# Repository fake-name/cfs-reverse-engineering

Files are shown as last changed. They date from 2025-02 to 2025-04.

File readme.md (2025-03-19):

Creality CFS Filament system Reverse Engineering

This is part of an effort to use the Creality CFS feeder system as a general AMS system for any Klipper-based printer.

This *should* be trivial, as the printer this normally interoperates with is also a Klipper-based machine. However, as usual, Creality are violating the GPL by not releasing their changes and additions to klipper (Creality implemented a custom bus type, and a bunch of utility bits to talk to the filament box).

Given that, the other option is reverse engineering how the feeder works. Fortunately, that should be pretty straightforward for most of the bits.

Anyways, high resolution board images are [here](PCBs.md).

Some attempts at analyzing the various binary firmware and python objects are [here](firmware.md)

Overall system structure:



The board can be flashed with klipper by just treating it as having a STM32F106VET6 (which is binary compatible with the GD32F303VET6). You loose a bit of potential clock-rate by not doing giga-device specific stuff, but this is fairly slow anyways so it should be fine. 

Specifying the klipper host connection to be on PA2/PA3 even works (albeit with RS485).

Current plan to convert the system to klipper in a neat way involves a simple interposer board to re-purpose the RS-485 lines:



The adapter board sits between the existing rear-panel connector and the existing controller board. It basically has 3 connectors, a CAN transciever, and a bypass capacitors. It simply carries all other signals + power through the PCB, but replaces the two RS-485 lines with CAN signalling. 

Since the IO needed to drive a CAN interface is exposed on the unused "J10" connector, that is connected to an appropriate CAN bus transciever IC (a [TCAN332G](https://www.ti.com/lit/ds/symlink/tcan332g.pdf)). 

The other end is another custom PCB. In this case, it's another custom PCB heavily inspired by the [candleLight FD](https://linux-automation.com/en/products/candlelight-fd.html) (read: I used some of their schematics for a starting point, the entire layout is my own work). It breaks out the CFS bus to a usb-CAN adapter (via [candleLight_fw](https://github.com/candle-usb/candleLight_fw) and the 24V power in via either a DC Barrel jack or a 2-pin micro-fit connector (there are pads for both on the PCB).

It also has a pair of LEDs to indicate buffer status, and some activity LEDs. 

Both boards are up at [Adapter](~/Adapter/). License for them is GPL3, since the candleLight FD is GPL3.

I had JLCPCB do the PCBs, they work out to ~$7 ea (CAN Adapter) and ~$10 ea (CFS-Bus Adapter), at qty 5 of each. I'm also trying LCSC's [custom-cable service](https://www.lcsc.com/customcables?utm_source=customcables&utm_medium=navbar) to make the short interposing cables, which wound up being ~$50 for 10 of each.

Full production files for each of the PCBs are in the respective folders, they should drag & drop into JLCPCB's PCBA service. The cables are based on a lot of guesswork about what the right connectors are, once I confirm I have the right part-numbers, I'll document that here as well.

Note that immediately after ordering the CFS-Bus-Adapter, I realized it would be super neat to allow the CAN transciever to be either connected to the CAN peripheral in the MCU (which is how it is now), and a UART interface. That would let this interact with the existing firmware if/when it get's properly reverse engineered, or Creality finally stops violating the GPL and provides the source for their [distributed-in-compiled-form-only klipper extensions](https://github.com/Guilouz/Creality-K2Plus-Extracted-Firmwares/tree/main/Firmware/usr/share/klipper/klippy/extras) (see all `.so` files, which are compiled with cython to make them opaque).

------

First rev board issues:

 - Pinout on J3 for CFS Can adapter board is reversed.   
   This can be fixed by just mirroring the routing of the jumper cable.
 - The open-collector buffer signals have pullups to 5V in the buffer. That means the buffer status LED resistors as implemented (i.e. between 24V and the buffer status pins) are effectively always on, since the 5V pullup winds up sinking current from the 24V LED rail.   
   This needs to be fixed by rev-ing the board (or with track hackery). Right now, the CFS buffer just changes the LED brightness, rather then turning them on and off.

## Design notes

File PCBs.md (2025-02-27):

# CFS Internal PCBs

## Main Motherboard
  
  

RS485 interface [3Peak TPT75176H](https://www.3peak.com/rs485/tpt75176h)
  

DC Motor Drivers: [HTD8236](https://offer-product.oss-cn-beijing.aliyuncs.com/product/offer/attachment/null/file/subPdf_749347_333113_20240123-141150640.pdf)
The use of the [LM358](https://www.ti.com/product/LM358) op amps are a mystery. Possibly current sensing? That would also align with the presence of the `R500` 500 mΩ resistors.   
Also present: a AMS1117 3.3v linear regulator. 
  

[24C16F EEPROM](https://ww1.microchip.com/downloads/en/DeviceDoc/Atmel-8719-SEEPROM-AT24C16C-Datasheet.pdf) in a SOT23-5 package.  
Q10 is probably a switch for the LCD's backlight LED?
  

Main CPU: [GD32F303](https://www.gigadevice.com/product/mcu/main-stream-mcus/gd32f30x-series/gd32f303) - STM32 ripoff ARM.
  

Brushless motor driver - [MS8828](https://www.relmon.com/en/index.php/list/detail/300.html). Made by [Ruimeng TECHNOLOGY](https://www.relmon.com)(sic). This part is interesting, because the firmware has references to a different part in some strings in it (`MS3791`)
  

## Pinouts:

### Connector types:
The majority of the connectors on the PCB are variants of the JST ["GH" connector style](https://www.jst.com/products/crimp-style-connectors-wire-to-board-type/gh-connector/), though not likely actually made by JST. 

All connectors other then the RS-485/Power (J4), the LCD (J15) and the filament monitor (J6) are GH-style. This includes the feeder motor connector (J5) which is indeed a GH connector, though with a right-angle-mount PCB connector.

##### J10 "Address" connector (not used?)

This connector is particularly interesting, since it is unused in the CFS configuration, and exposes the USB pins of the MCU. That means it should be possible to make up a USB cable. Alternatively, it also exposes the CAN pins.

The USB interface is annoying in that the MCU documentation specifies approximately 50Ω series termination resistors on both the DM and DP pins, which are not present. It may be possible to add these resistors in-line with the cable. I need to do some experiments.

PA4,6,7 don't have any features that seem to make them of particular interest. 

Annoyingly, the Gigadevices USB interface documentation is really terrible, and you also need a 1.5KΩ resistor between D+ and VCC (or a MCU IO pin). Once I added that (to PC6), and told klipper to pull the pin high at boot, the USB interface started working.

| Pin #  |  Function | MCU Pin No | Logical Pin | Note |
| ---| --- | --- | --- | --- |
| 1 | power | 3.3V | | |
| 2 | | P.70 | PA11 | USBDM / CAN0_RX |
| 3 | | p.71 | PA12 | USBDP / CAN0_TX |
| 4 | | p.31 | PA6 | |
| 5 | | p.32 | PA7 | |
| 6 | | p.29 | PA4 | |
| 7 | power | GND | | |

##### J4 (Power/Comm Connector)
 
| Pin #  | Function | MCU Pin No | Logical Pin |
| --- | --- | --- | --- |
| 1 | +24V | n/a | |
| 2 | +24V | n/a | |
| 3 | GND | n/a | |
| 4 | GND | n/a | |
| 5 | RS485-B | see note | |
| 6 | RS485-A | see note | |
| 7 | Filament Buffer SW 1 | p.55 | PD8 |
| 8 | Filament Buffer SW 2 | p.56 | PD9 |
The 485 bus uses 3 pins:
 
 - P.25 (PA2) - TX Enable/RX Disable - 2N7002 translator
 - P.26 (PA3) - RX
 - TX - I think strapped to ground. 

This is I believe technically violating RS-485 specs.

This device, like many crappy chinese "RS-485" systems, does not *really* support RS485. Instead, the bus is run in a pseudo-differential-open-collector mode (much like CAN networks), in that the transmitter is permanently wired up as "transmitting", e.g. the "space" mode, and rely on the bus termination resistors to drive the bus back to the idle "mark" state. Aside from not being real RS-485, this STRONGLY limits the maximum baud-rate the bus due to the fact that the only termination resistors present on the PCB are two 300Ω resistors, with `A` pulled to VCC (5V) and `B` pulled to ground.

While there is a provision for a 120Ω termination resistor on the board, it is not loaded on the board I have.

I *believe* this connector is a SMW200-08, (Yeonho SMW). 

It is a 2 mm pitch, latching connector, and the full-width latch catch on the PCB-mount connector is fairly distinct.

##### J15 (FP LCD Connector)

| Pin #  |  Function | MCU Pin No | Logical Pin |
| ---| --- | --- | --- |
| 1 | power | 3.3V | |
| 2 | power | GND | |
| 3 | | p.16 | PC1 |
| 4 | | p.17 | PC2 |
| 5 | | p.18 | PC3 |
| 6 | | p.33 | PC4 |
| 7 | backlight | P.35 | PB0 |

Note: The backlight pin is a open collector transistor.

I *believe* this connector is a SMW200-07, (Yeonho SMW). 

It is a 2 mm pitch, latching connector, and the full-width latch catch on the PCB-mount connector is fairly distinct.

The power-in connector (J4) is the same series.

##### J7 Front-Panel LED PCB Connector

| Pin #  |  Function | MCU Pin No | Logical Pin | Function |
| ---| --- | --- | --- | --- |
| 1 | power | 5.0V | | |
| 2 | | p.63 | PC6 | Slot 1 Red LED |
| 3 | | p.93 | PB7 | Slot 1 White LED |
| 4 | | p.64 | PC7 | Slot 2 Red LED |
| 5 | | p.90 | PB4 | Slot 2 White LED |
| 5 | | p.65 | PC8 | Slot 3 Red LED |
| 6 | | p.91 | PB5 | Slot 3 White LED |
| 7 | | p.66 | PC9 | Slot 4 Red LED |
| 8 | | p.92 | PB6 | Slot 4 White LED |
| 10 | power | GND | | |

Note: All LED connectors are Open-Collector Transistors.
Presumably, the LEDs are between 5V and the various open-collector
outputs.

Interestingly, the red LEDs for slots 2 & 3 seem to be the same pin. 

This is a 10 pin connector, but I somehow missed a pin somewhere. 

##### Motor driver pins

|  Driver pin  | M1 | M2 | M3 | M4 |
| --- | --- | --- | --- | --- |
| IN 1 | p.84 (PD3) | p.82 (PD1) | p.62 (PD15) | p.60 (PD13) |
| IN 2 | p.83 (PD2) | p.81 (PD0) | p.61 (PD14) | p.59 (PD12) |

##### Current Feedback Pins

| Motor |  Pin | Logical Pin |
| --- | --- | --- |
| M1 | p.34 | PC5 |
| M2 | p.15 | PC0 |
| M3 | p.24 | PA1 |
| M4 | p.23 | PA0 |

Each feedback pin is driven by an op-amp with some gain and a offset shift.

##### Brushed Motor connector / J5

| Pin #  |  Function | MCU Pin No | Logical Pin |
| ---| --- | --- | --- |
| 1 | I2C? | P.79 |  PC11 |
| 2 | Power | GND | |
| 3 | I2C? | p.80 |  PC12 |
| 4 | | p.88 |  PD7 |
| 5 | | p.87 |  PD6 |
| 6 | | p.86 |  PD5 |
| 7 | | p.85 |  PD4 |
| 8 | Power | 5V | |
| 9 | | M4-Out1 | |
| 10 | | M4-Out2 | |
| 11 | | M3-Out1 | |
| 12 | | M3-Out2 | |
| 13 | | M2-Out1 | |
| 14 | | M2-Out2 | |
| 15 | | M1-Out1 | |
| 16 | | M1-Out2 | |

Pins 1 & 3 have 2N7002 discrete level translators to go from 5V I2C to 3.3V MCU I2C, I believe. They connect thru to the Temp/Humidity measurement I2C sensor in the chamber. 

##### RFID Readers / J8 / J1

| Pin #  |  Function | J8 | J19 |
| ---| --- | --- | --- |
| 1 | Power | 3.3V | |
| 2 | I2C? | p.48 (PB11) | p.96 (PB9)  |
| 3 | Power | GND | |
| 4 | I2C? | p.47 (PB10) | p.95 (PB8)  |
| 5 | Power | GND | |
| 6 | | N/C? | |

Pin 6 on both seems to be not-connected, surprisingly.

##### J6 - Odometer and second-stage filament presence detector

| Pin #  |  Function | MCU Pin No | Logical Pin |
| ---| --- | --- | --- |
| 1 | Power | 3.3V | |
| 2 | | p.46 |  PE15 |
| 3 | | p.53 |  PB14 |
| 4 | | p.54 |  PB15 |
| 5 | | p.52 |  PB13 |
| 6 | | p.51 |  PB12 |
| 7 | | p.89 |  PB3 |
| 8 | Power | Gnd | |
| 9 | | p.38 |  PE7 |
| 10 | | p.39 |  PE8 |
| 11 | | p.40 |  PE9 |
| 12 | | p.41 |  PE10 | 

Pins 9-12 have R/C filters on them. My current guess is they are 
the filament presennce paths, while the other 6 are for the odometer.

Hopefully I can extend https://github.com/Klipper3d/klipper/pull/5369 to support the odometer.

##### BLDC Motor Driver:

| Driver Func | MCU Pin No | Logical Pin |
| --- | --- | --- |
| SS | p.03 | PE4 |
| FG | p.42 | PE11 |
| F/R | p.02 | PE3 |
| PWM | p.44 | PE13 |

FG is a tachometer output from the driver. SS is motor brake, F/R is forward/reverse, PWM is speed control (obviously).

### RFID Readers:

[FM17622](https://eng.fmsh.com/AjaxFile/DownLoadFile.aspx?FilePath=/UpLoadFile/20190410/FM17510_ps_eng.pdf&fileExt=file) - Supports most protocols and interfaces. 13.56 MHz (I think?)
  

  

Both RFID readers are identical.
  

### LCD 

Front-Panel LCD - [TM1621B](https://wmsc.lcsc.com/wmsc/upload/file/pdf/v2/lcsc/2209231730_TM-Shenzhen-Titan-Micro-Elec-TM1621B_C5174490.pdf) - Stand-Alone LCD driver, no MCU. 
  

### Connector PCB
  

Cable colors

 - Yellow - 24V
 - Green - GND
 - Blue - 485
 - Red - 485
 - White - sw?
 - Black - sw?

### Filament sensor PCB

Forgot to take pictures of the other side of the board.
  

### Filament feeder assembly

This is partly a pass-thru to the filament sensor PCB (above). 

It also has a MagnTek [MT6826S](https://www.magntek.com.cn/upload/pdf/202407/MT6826S_Datasheet_Rev.1.1.pdf). 
  

  

### Filament 4-into-1 buffer PCB.
  
  

The 4-into-1 PCB is very dumb, it just has 2 open-collector outputs that correspond to each optointerruptor. One for each end of the buffer-state.

All the parts on the board are just a DC-DC converter to produce a local power supply from the 24V bus. 

Since all CFS boxes will have access to the buffer state pins, whichever one is currently active in feeding to the print head can autonomously keep the buffer loaded without needing the printer controller's involvement.

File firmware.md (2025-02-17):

Firmwares:

MCU Firmware files are taken from [here](https://github.com/Guilouz/Creality-K2Plus-Extracted-Firmwares/tree/main/Firmware/usr/share/klipper/fw/cfs). In particular, I'm examining `cfs0_050_G32-cfs0_000_113.bin`, admittedly for no particular reason other then it seems the most current version.

Just throwing the firmare into `strings already produces a LOT of really interesting snippets:

```
 \ | /
- RT -     Thread Operating System
15:19:29
Jan  6 2025
 / | \     %d.%d.%d build %s %s
 2006 - 2022 Copyright by RT-Thread team
```
Interestingly, the MCU does not run a klipper based system. Instead, it seems to be based on RT-Thread, which is a primarily Chinese-origin RTOS. 

RT-Thread is apache licensed (not copyleft), but it does require attribution, and interestingly searching for `"creality" "rt-thread"` returns no meaningful results, so creality seems to have managed to even violate a bsd-style license!

Ghidra gives us the full version info:

```
    debug_print(s_\_|_/_08018378);
    debug_print(s_-_RT_-_Thread_Operating_System_08018384);
    debug_print(s_/_|_\_%d.%d.%d_build_%s_%s_080183c0,5,0,2,s_Jan_6_2025_080183b4,s_15:19:29_080183a8);
    debug_print(s_2006_-_2022_Copyright_by_RT-Thre_080183e4);
```

So this is based on RT-thread 5.0.2, built on `Jan_6_2025` at `15:19:29`. 5.0.2 was released
on Oct 7, 2023, so they're a bit behind in updating the copyrights in the code if nothing else.

There's also a LOT of debug/informational statements:

```

feeder reverse detooth slot_id:%d
hub reverse update [dir:%s, speed:%d]
feeder reverse detooth force
detooth update [dir:%s, speed:%d]
MS3791 is overload
motor_blocked_detect_timer
pull back hub PE retry:%d
pull back hub PE timeout, retry times exhausted
times:%d, %d error,T%d AT8236 and MS3791 push filament timeout
#<times:%d, %d error,T%d pull_back_hub motor block, state=%02x
perhaps pull back odometer
already pull back odometer
etc...
```

In particular, there appear to be at least the remaining stubs of a interactive interface:

```
slot%d read rfid and margin estimation
preloading
read
enable
disable
aging
Usage: 
preloading enable            - enable preloading
preloading disable           - disable preloading
preloading aging             - aging preloading
preloading read [slot_id]    - read filament info
```

```
Usage: 
bl24cxx init                            - init bl24cxx
bl24cxx capacity                        - bl24cxx get capacity
bl24cxx ready                           - bl24cxx is ready?
bl24cxx deadlock <address>              - bl24cxx deadlock
bl24cxx undeadlock                      - bl24cxx undeadlock
```

```
Usage: 
odo_mag init            - init magnetic odometer
odo_mag test            - test magnetic odometer communication
odo_mag monitor [en]    - print magnetic odometer positon
odo_mag reset           - reset magnetic odometer
odo_mag read step       - read raw value of magnetic odometer
odo_mag read mm         - read position of magnetic odometer
```

Having what are basically help strings in the generated firmware image is interesting. 

There are also a number of situations where there are strings with VT100 control characters in them:`[31m[E/odometer_magnetic]`, `[0m[D/odometer_magnetic]`, `[31m[E/preloading]`, etc... I suspect there may be a debug UART somewhere.

It seems unlikely to me that all the debug strings are fed back over the RS485 port, in particular considering that there can be up to 4 of these things sharing a single RS485 bus. 

There's also some super weird stuff:

`database checksum error, load default value ...`

I have no idea what a "database" would be in the context of a embedded MCU with no real storage space. My best guess is it's something related to the I2C EEPROM. There are also supporting strings: `read_motor_info eeprom                  - read motor block info from eeprom`.

I suspect there are a number of locations where weird terminology is more a function of poor translation. There are a lot of references to `<something>_aging` in various places, which I suspect may be ore accurately stated as a timeout or latency.

------

So I've been going through and naming function stubs, working through the decompilation of the MCU source, and things are starting to make some sense. They are definitely measuring the motor current for the brushed DC motors:

```
        rt_kprintf(s_current_channel_=_%d_0800445b + 1,uVar3);
        FUN_080073e8();
        FUN_0800c0fc(0xff);
        iVar1 = _DAT_08004474;
        while (fVar5 = (float)FUN_0800725a(), iVar2 = _DAT_08004490, (int)ABS(fVar5) < iVar1)
        {
            iVar2 = FUN_08003aa8(uVar3,0,5);
            if (iVar2 != 0)
            {
                rt_kprintf(s_AT%d_pull_out,_restart_08004476 + 2,uVar3);
                FUN_0800c130();
                goto LAB_0800425c;
            }
            FUN_08019cc0(10);
        }
```

------

Empirically, connecting to the MCU with a debugger and poking it while it's running let's me determine whether it's primarily running from main flash (`0x0800_0000`), rather then the mirror (`0x0000_0000`). 

```
0x0800066e in ?? ()
─── Assembly ──────────────────────────────────────────────────────────────────────────
 0x0800066e  ? ldr      r0, [r1, #0]
 0x08000670  ? str      r2, [r1, #0]
 0x08000672  ? cmp      r0, r2
 0x08000674  ? ittt     hi
 0x08000676  ? ldrhi    r0, [r3, #0]
 0x08000678  ? addhi.w  r0, r0, #16777216       ; 0x1000000
 0x0800067c  ? strhi    r0, [r3, #0]
 0x0800067e  ? ldr      r0, [r3, #0]
 0x08000680  ? movw     r3, #15000      ; 0x3a98
 0x08000684  ? udiv     r0, r0, r3
─── Breakpoints ───────────────────────────────────────────────────────────────────────
─── Expressions ───────────────────────────────────────────────────────────────────────
─── History ───────────────────────────────────────────────────────────────────────────
─── Memory ────────────────────────────────────────────────────────────────────────────
─── Registers ─────────────────────────────────────────────────────────────────────────
       r0 0x000009d4        r1 0x20000b28          r2 0x0040103b        r3 0x20000c80
       r4 0x00007530        r5 0x20000010          r6 0x20000918        r7 0x08002224
       r8 0x08002208        r9 0x08002224         r10 0x00000001       r11 0x00000002
      r12 0x00ffffff        sp 0x2000fef0          lr 0x08001437        pc 0x0800066e
     xPSR 0x01000000     fpscr 0x00000000         msp 0x2000fef0       psp 0x20003af8
  primask 0x00         basepri 0x00         faultmask 0x00         control 0x00
─── Source ────────────────────────────────────────────────────────────────────────────
─── Stack ─────────────────────────────────────────────────────────────────────────────
[0] from 0x0800066e
[1] from 0x08001436
─── Threads ───────────────────────────────────────────────────────────────────────────
[1] id 0 from 0x0800066e
─── Variables ─────────────────────────────────────────────────────────────────────────
───────────────────────────────────────────────────────────────────────────────────────
>>>

```

Across multiple samples `0x08001436` seems consistently present in the stack. 

Looking up what is at that location, it looks reasonable for a main loop:

```
undefined4 main_func_maybe(uint param_1)
{
    char cVar1;
    uint uVar2;
    int iVar3;
    ushort local_32;
    undefined4 local_30;
    undefined4 auStack_2c [7];
    
    local_30 = 0;
    setup_func_one(auStack_2c,0,0x1c);
    local_32 = 0;
    if (param_1 != 0xffffffff)
    {
        setup_func_two();
    }
    do
    {
        if ((param_1 != 0xffffffff) && (uVar2 = FUN_08000650(), param_1 < uVar2))
        {
            return 0xffffffff;
        }
        iVar3 = DAT_20000b18;
        if ((((iVar3 != 0) && (uVar2 = FUN_08000130((int)&local_30,&local_32), 1 < (uVar2 & 0xff))) && (local_32 == 2)) &&
           (((local_30._1_1_ == '\v' && (local_30._2_1_ == '\x01')) && (iVar3 = FUN_08000a38(), iVar3 == 1))))
        {
            FUN_08001304();
        }
        cVar1 = DAT_20000010._0_1_;
    } while (cVar1 == -2);
    return 0;
}
```

It's true that this could very likely be the primary idle loop. Now, since this is a RTOS, we will likely have other threads that are just either not active (because we're not actively sending serial traffic), or just generally not executing (Sampling here is done by just stopping and restarting in GDB by hand multiple times. Low-duty cycle execution contexts are unlikely to be observed).

------

Complete strings listing (trimmed a bit for for things that are obviously not real strings):

```
 sn_information=%s
heartbeat
preload
rs485
print_check
 current mode = %d
 485 uid = %d
15:19:26
Jan  6 2025
MF003 V%d.%d.%d build %s %s
[33m[W/system] 
feeder reverse detooth slot_id:%d
hub reverse update [dir:%s, speed:%d]
feeder reverse detooth force
detooth update [dir:%s, speed:%d]
===================================
motor info:
block
noblock
feeder0 %s
feeder1 %s
feeder2 %s
feeder3 %s
hub %s
slot_id=%d
Bfeeder_curr_voltage=%d.%02dV
feeder_thrust_voltage=%d.%02dV
feeder_resistance_voltage=%d.%02dV
feeder_target_speed=%d
feeder_pid_output=%d
feeder_dir=%s
hub_target_speed=%d.%02drps
hub_curr_speed=%d.%02drps
hub_pid_output=%d
hub_dir=%s
reverse detooth timeout, %dms
is_reverse_detooth
MS3791_is_blocked
MS3791 is overload
MS3791 is overload
motor_blocked_detect_timer
feeder_reverse_detooth_reenable_timer
#<feeding stop, odometer not change
@Judge attempt: %d
sec remaining: %d
Retry attempt: %d
%s: last_odom = %d.%02dmm
%s: odom - last_odom = %d.%02dmm
%s: %d!
illegal data
 pull back hub PE timeout
already pull back hub PE
pull back hub PE retry:%d
pull back hub PE timeout, retry times exhausted
#<pull_back_hub motor block, state=%02x
pull back odometer retry:%d
pull back odometer timeout
already pull back odometer
cmd_parse_out %d!
 --------------------out ret = %d
buffer_fill_timeout
forced_preloading %d
 forced_preloading!
 reverse_detooth_set [en] 
origin reverse_detooth_en = %d
new reverse_detooth_en = %d
realtime
eeprom
Usage: 
 eeprom_init_flag: %d
AHTxx_init_flag: %d
odometer_magnetic_init_flag: %d
Buffer_init_flag: %d
rfid_init_flag[0]: %d; rfid_init_flag[1]: %d
[31m[E/preloading] 
pretension hub insert fil detect timeout
pretension hub pullout fil detect timeout
[0m[D/preloading] 
%d realtime insert
%d realtime pullout
%d finish action
== first detect a card
other_slot_id FEEDER_DIR_IN
other_slot_id FEEDER_DIR_OUT
(rfid move)hub pullout fil detect timeout
rfid has a card
move count:%d
first detect success
==detect multi cards
margin_estimation_and_read_rfid feed hub timeout
hub move count:%d
[33m[W/preloading] 
margin estimation timeout, plese check the odometer of hub
[32m[I/preloading] 
detect rfid:%d
different rfid uid detected, retry ...
-------------------------------------------
the number of RFID retries read message is exhausted
 rfid continuous detect timeout, plese move next the slot
Crfid detected next to it, move it
the number of RFID retries next to the move is exhausted
 slot%d insert filament
[32m[I/preloading] 
slot%d pullout filament
presd
 slot%d start preloading
slot%d pretension
STATE_CHECK_HUB
hub has filament
slot%d read rfid and margin estimation
preloading
read
enable
disable
aging
Usage: 
preloading enable            - enable preloading
preloading disable           - disable preloading
preloading aging             - aging preloading
preloading read [slot_id]    - read filament info
is busy=%d
slot%d =====================================
    has filament=%d
    has rfid=%d
    filament percent=%d%%
    rfid_base
        month=%c
        day=%.*s
        year=%.*s
        supplier=%.*s
        batch=%.*s
        mat_id=%.*s
        col=%.*s
        len=%.*s
        number=%.*s
        reserve=%.*s
        flag=%d
    rfid_high
B        len=%d.%02d
 =====================
RFID reader id: %d 
test count: %d, 
card found count: %d, 
card found fail: %d
read pass count: %d, 
read fail count: %d
 sensor_init_fail!
 host_temp = %d, slave_temp = %d
host_hum = %d, slave_hum = %d
sensor_test_fail!
 current channel = %d
 AT%d pull out, restart
8T%d feed finish, start pull back
T%d pull back finish, wait for pull out
finish test
all count: %d
card found count: %d
read pass count: %d
========ERROR========
RED%d_CTL
BLUE%d_CTL
LIMIT_%d
BUF_LIMIT_1: PD8
BUF_LIMIT_2: PD9
 %d vol:%d.%03dV  
<IDETA_ADC_MCU:PC5
YA_PWM_1:PD2
YA_PWM_2:PD3
IDETB_ADC_MCU:PC1
YB_PWM_1:PD0
YB_PWM_2:PD1
IDETC_ADC_MCU:PA1
YC_PWM_1:PD14
YC_PWM_2:PD15
IDETD_ADC_MCU:PA0
YD_PWM_1:PD12
YD_PWM_2:PD13
==================MOTHER BOARD test==================
EEPROM_SCL:PE5
EEPROM_SDA:PE6
SCL2:PB8
SDA2:PB9
SCL1:PB10
SDA1:PB11
Look at the BLDC
FG1:PE11
PWM:PE13
BRAK:PE4
F&F%FO
AHT30_SCL_3V:PC11
AHT30_SDA_3V:PC12
SPI_CS:PB12
SPI_CK:PB13
SPI_MISO:PB14
SPI_MOSI:PB15
=====================FINISH TEST=====================
slot%d trigger success:%d
buffer error,please check connect and board
 error_full:%d, error_empty:%d
free_count:%d, full_count:%d, to full: %dms, to free: %dms
buffer component error !
dir = out, up; time = %d ms, count = %d
dir = back, up; time = %d ms, count = %d
dir = out, down; time = %d ms, count = %d
dir = out, down; time = %d ms
============================
BLDC gravity aging mode count = %d
BLDC_aging_test finished, count = %d
filament in channel%d
out ok
 back ok
 RFID_authentication
switch mode:%d
switch standard mode!
Cillegal mode!
switch_mode [mode]
print_buffer_aging
Current mode is not support this command
free_count:%d, full_count:%d
aging_photoelectric_CMD [first_id] [end_id]
[%d] %s: ch: %d ready !
==============================
try to move into reader timeout
read RFID message failed
try to move out reader timeout
ch = %d, in reader area time = %d ms, circle time = %d ms
 switch to STANDARD_MODE
 init
temp
slave_num
light
Usage: 
lcd init                   					-lcd init to 0
lcd hum     <hum>  									-lcd set hum, such as 'lcd hum 31'
lcd slave_num <slave_num>          -lcd set slave number
lcd light   <0/1>  									-lcd set light open/off
[0m[D/RS485_AUTO_ADDR] 
error package->head is %02X
package_crc is %02X, cal_crc is %02X
sda=%d, scl=%d
 init
 ready
undeadlock
deadlock
capacity
write
read
bl24cxx_is_ready:%d
Please using 'bl24cxx init' first.
bl24cxx_get_capacity:%d
bl24cxx_write_bytes:address=%d, data=%d
bl24cxx_read_bytes:address=%d, data=%d
Usage: 
bl24cxx init                            - init bl24cxx
bl24cxx capacity                        - bl24cxx get capacity
bl24cxx ready                           - bl24cxx is ready?
bl24cxx deadlock <address>              - bl24cxx deadlock
bl24cxx undeadlock                      - bl24cxx undeadlock
Bodometer_magnetic current position:%d.%02dmm
[0m[D/odometer_magnetic] 
success
fail
read userid %s, id=0x%02x
[31m[E/odometer_magnetic] 
odometer_magnetic_init communication fail
odometer_magnetic_init mt6826_timer create fail
init
reset
test
monitor
read
Please using 'odo_mag init' first.
odo_mag communication %s
step
Usage: 
odo_mag init            - init magnetic odometer
odo_mag test            - test magnetic odometer communication
odo_mag monitor [en]    - print magnetic odometer positon
odo_mag reset           - reset magnetic odometer
odo_mag read step       - read raw value of magnetic odometer
odo_mag read mm         - read position of magnetic odometer
odometer_magnetic current step:%d
 SetReg: send RFID_ADDR failed!
SetReg: send reg_addr failed!
SetReg: send data failed!
GetReg: send RFID_ADDR failed!
GetReg: send reg_addr failed!
GetReg:  RFID_ADDR read failed!
rfid[%d] softReset failed, reg_data = %x!
 ReaderA_Select: rfid[%d] reg_data = %x
 card %d auth block %d failed, reg_data = %x
card %d card_write:JREG_FIFOLEVEL reg_data = %d
card %d card_write 2:JREG_FIFOLEVEL reg_data = %d
card_write: block num %d is error!
card %d card_write 2:JREG_FIFODATA reg_data = %d
card_read: block num %d is error!
card %d card_read: reg_data = %d
can't find %s device!
read aht10 sensor humidity   : %d.%d %%
read aht10 sensor temperature: %d.%d
initialize sensor failed!
dbg_temp = %d, dbg_humi = %d
 detooth_test [id] [dir]
id is between 0 to 3
dir illegal
card read failed!
 228241200A1
1010010FF0000
0330000001000000
rfid_init_info_read %d, %d
 read vector %d is failed!
------------base %d info-------------
%s is 
 read vector 8 is failed!
------------high %d info-------------
now length = %d
 busy
none
unknown
init
 write
read
show
Usage: 
rfid init     <card id>               -rfid connect card
Please using 'rfid init <card id>' first.
base
high
RCrfid read     <card id>  <base/high>  -rfid card read data
read failed!
 status = %d
[32m[I/RS485] 
find %s success!
[31m[E/RS485] 
init %s failed!
init %s success!
open %s failed!
find %s failed!
 uid = %d
 preload_check_flag = 1, heartbeat update
 enable buffer!
disable buffer!
 heartbeat
 heartbeat_wait ret = %d
 rs485_lb
rs485 timeout, %d
 box status:
STATE_IDLE
STATE_PRELOAD
STATE_PRINT
STATE_RELOAD
STATE_ERROR
STATE_TEST
unknown
task_tset [0(out)/1(back)/2(out+back)] [motor_id] [times]
get device uid=0x%02x
protocol_dev.status=%d
Bmotor%d, average_vol=%d.%02d, starting_vol=%d.%02d
[32m[I/AT8236] 
find %s device!
[31m[E/AT8236] 
pwm run failed! can't find %s device!
adc run failed! can't find %s device!
 at8236_test id=%d speed=%d dir=%d
at8236(%d) voltage=%d.%02d
voltage(%d)=%d.%02d, voltage(%d)=%d.%02d
adct
 at8236 adc timer ok
at8236_pid_set outkp=%d outki=%d outkd=%d bkp=%d bki=%d bkd=%d
 motor_id = %d, led set err %x
 led_test col=%d id=%d, open=%d
tim_rotational_speed_detect
pwm1
[32m[I/MS3791] 
find MS3791 enable device!
[31m[E/MS3791] 
pwm run failed! can't find MS3791 enable dev!
MS3791_test speed=%d dir=%d
MS3791_time_test [dir] [speed] [time_ms]
dir is 0 or 1
speed is between 0 to 255
MS3791_time_test dir = %d speed = %d time_ms = %d
Bmove position = %d.%02dmm
 MS3791_read_fg pluse=%d
 ms3791_pid_set kp=%d.%02d ki=%d.%02d kd=%d.%02d
 buffer free!
buffer full!
Bodom first:%d.%02dmm,now=%d.%02dmm,diff:%d.%02dmm
 err 0x52!--1
 Berr 0x51
init buffer irq
 buffer status = %d
fmc_word_program fail. ret = %d, data = 0x%x
 %s: can't find the key: %d 
[33m[W/db_key_handler] 
database checksum error, load default value ...
?times:%d,T%d test_fixture %d ok
times:%d, %d error, pull back other filaments timeout!
T%d out start
times:%d, %d error,T%d out timeout!
feed: ch = %d, motor max voltage = %d.%02d v
last_odom = %d.%02dmm
odom - last_odom = %d.%02dmm
times:%d, %d error,T%d AT8236 and MS3791 push filament timeout
#<times:%d, %d error,T%d pull_back_hub motor block, state=%02x
perhaps pull back odometer
already pull back odometer
times:%d, %d error,T%d pull_back_hub timeout
times:%d, %d error,T%d back timeout!
back: ch = %d, motor max voltage = %d.%02d v
box aging finish all channel
 box_aging_mode_test [first_channel] [end_channel] [times]
channel ranges from 0 to 3
[33m[W/armlibc.syscalls] 
Please enable RT_USING_POSIX_FS
[33m[W/stdlib] 
thread:%s exit:%d!
 bus fault:
SCB_CFSR_BFSR:0x%02X 
IBUSERR 
PRECISERR 
IMPRECISERR 
UNSTKERR 
STKERR 
SCB->BFAR:%08X
psr: 0x%08x
r00: 0x%08x
r01: 0x%08x
r02: 0x%08x
r03: 0x%08x
r04: 0x%08x
r05: 0x%08x
r06: 0x%08x
r07: 0x%08x
r08: 0x%08x
r09: 0x%08x
r10: 0x%08x
r11: 0x%08x
r12: 0x%08x
 lr: 0x%08x
 pc: 0x%08x
hard fault on thread: %s
hard fault on handler
FPU active!
failed vector fetch
debug event
usage fault:
SCB_CFSR_UFSR:0x%02X 
UNDEFINSTR 
INVSTATE 
INVPC 
NOCP 
UNALIGNED 
DIVBYZERO 
mem manage fault:
SCB_CFSR_MFSR:0x%02X 
IACCVIOL 
DACCVIOL 
MUNSTKERR 
MSTKERR 
SCB->MMAR:%08X
 %bp
dev != RT_NULL
rt_object_get_type(&dev->parent) == RT_Object_Class_Device
rt_object_is_systemobject(&dev->parent)
rt_object_is_systemobject(&dev->parent) == RT_FALSE
[31m[E/kernel.device] 
To initialize device:%s failed. The error code is %d
dev->ref_count != 0
[33m[W/hwtimer] 
frequency setting out of range! It will maintain at %d Hz
timer != RT_NULL
timer->ops != RT_NULL
timer->info != RT_NULL
[33m[W/I2C] 
wait ack timeout
[31m[E/I2C] 
ACK or NACK timeout.
NACK: sending first addr
NACK: sending second addr
NACK: sending repeated addr
send bytes: error %d
i2c_bus_lock
[32m[I/I2C] 
I2C bus [%s] registered
[31m[E/I2C] 
I2C bus %s not exist
I2C bus operation not supported
bus != RT_NULL
bus != RT_NULL
buffer != RT_NULL
completion != RT_NULL
Function[%s]: scheduler is not available
Function[%s]: interrupt is disabled
Function[%s] shall not be used before scheduler start
Function[%s] shall not be used in ISR
rt_list_isempty(&(completion->suspended_list))
queue != RT_NULL
size > 0
queue->magic == DATAQUEUE_MAGIC
Function[%s]: scheduler is not available
Function[%s]: interrupt is disabled
Function[%s] shall not be used before scheduler start
Function[%s] shall not be used in ISR
data_ptr != RT_NULL
size != RT_NULL
ops != RT_NULL && ops->convert != RT_NULL
probe
 enable
read
disable
voltage
Unknown command. Please enter 'adc' for help
adc probe <device name>   - probe adc by name
success
probe %s %s 
failure
Please using 'adc probe <device name>' first
adc enable <channel>   - enable adc channel
%s channel %d enables %s 
adc read <channel>     - read adc value on the channel
%s channel %d  read value is 0x%08X 
adc disable <channel>  - disable adc channel
%s channel %d disable %s 
adc convert voltage <channel> 
%s channel %d voltage is %d.%03dV 
Usage: 
adc probe <device name> - probe adc by name
adc read <channel>      - read adc value on the channel
adc disable <channel>   - disable adc channel
adc enable <channel>    - enable adc channel
pin != RT_NULL
_hw_pin.ops != RT_NULL
pin [option] GPIO
     num:      get pin number from hardware pin
               e.g. MSH >pin mode GPIO output
     read:     read pin level of hardware pin
               e.g. MSH >pin read GPIO
               e.g. MSH >pin write GPIO high
     help:     this help list
GPIO e.g.:
output
input
input_pullup
input_pulldown
output_od
Parameter invalid : %s!
mode
read
write
Parameter invalid : %s!
probe
 enable
disable
phase
dead_time
Usage: 
pwm phase      <channel> <phase>            - set pwm phase
pwm probe <device name>                  - probe pwm by name
success
probe %s %s
failure
Please using 'pwm probe <device name>' first.
pwm enable <channel>                     - enable pwm channel
    e.g. MSH >pwm enable  1              - PWM_CH1  nomal
%s channel %d is enabled %s 
pwm disable <channel>                    - disable pwm channel
Get info of device: [%s] error.
Info of device [%s] channel [%d]:
period      : %d
pulse       : %d
Y@Duty cycle  : %d%%
Set info of device: [%s] error
Usage: pwm set <channel> <period> <pulse>
pwm info set on %s at channel %d
%s phase is set %d 
%s dead_time is set %d 
pwm probe      <device name>               - probe pwm by name
pwm phase      <channel> <phase>           - set pwm phase
pwm dead_time  <channel> <dead_time>       - set pwm dead time
[33m[W/UART] 
rx_fifo != RT_NULL
(serial != RT_NULL) && (data != RT_NULL)
rx_dma != RT_NULL
serial->ops->dma_transmit != RT_NULL
dev != RT_NULL
tx_fifo != RT_NULL
tx_dma != RT_NULL
serial != RT_NULL
serial->parent.rx_indicate != RT_NULL
tx != RT_NULL
len <= rt_dma_calc_recved_len(serial)
[31m[E/drv.adc] 
invalid channel
@invalid param
 failed register %s, err=%d
@invalid cmd:%x
failed register %s, err=%d
[31m[E/DBG] 
Can not find -1 of gd32_periph_list's member of Port!
Can not find -1 of gd32_periph_list's member of TimerIndex!
@Unsport timer periph!
%s register failed
[31m[E/DBG] 
Unsport gpio port!
Unsport timer periph!
result == RT_EOK
uart != RT_NULL
 serial != RT_NULL
cfg != RT_NULL
uart1
result == RT_EOK
shell != RT_NULL
finsh: can not find device: %s
tshell
shrx
no memory for shell
RT-Thread shell commands:
 %-16s - %s
total    : %d
used     : %d
maximum  : %d
available: %d
%s: command not found.
%-16s - %s
    %-16s - %s
retp
Too many args ! We only Use:
thread
rt_thread_t
%-*.*s 
 ---  ------- ---------- ----------  ------  ---------- ---
%-*.*s %3d 
 suspend
 ready  
 init   
 close  
 running
 0x%08x 0x%08x    %02d%%   0x%08x %s
semaphore
%-*.*s v   suspend thread
 --- --------------
%-*.*s %03d %d:
%-*.*s %03d %d
event
%-*.*s      set    suspend thread
  ---------- --------------
%-*.*s  0x%08x %03d:
%-*.*s  0x%08x 0
mutex
%-*.*s   owner  hold priority suspend thread 
 -------- ---- -------- --------------
%-*.*s %-8.*s %04d %8d  %04d 
%-*.*s %-8.*s %04d %8d  %04d
':F#F
!}#F
 `%r
mailbox
%-*.*s entry size suspend thread
 ----  ---- --------------
%-*.*s %04d  %04d %d:
%-*.*s %04d  %04d %d
msgqueue
%-*.*s entry suspend thread
 ----  --------------
%-*.*s %04d  %d:
%-*.*s %04d  %d
timer
%-*.*s  periodic   timeout    activated     mode
 ---------- ---------- ----------- ---------
%-*.*s 0x%08x 0x%08x 
activated   
deactivated 
periodic
one shot
current tick:0x%08x
device
%-*.*s         type         ref count
 -------------------- ----------
Unknown
%-*.*s %-20s %-8d
 Usage: list [options]
[options]:
%.*s
main
tid != RT_NULL
sem != RT_NULL
value < 0x10000U
(flag == RT_IPC_FLAG_FIFO) || (flag == RT_IPC_FLAG_PRIO)
rt_object_is_systemobject(&sem->parent.parent)
Function[%s] shall not be used in ISR
rt_object_is_systemobject(&sem->parent.parent) == RT_FALSE
 Function[%s]: scheduler is not available
Function[%s]: interrupt is disabled
Function[%s] shall not be used before scheduler start
mutex != RT_NULL
rt_object_is_systemobject(&mutex->parent.parent)
rt_object_is_systemobject(&mutex->parent.parent) == RT_FALSE
 event != RT_NULL
rt_object_is_systemobject(&event->parent.parent)
rt_object_is_systemobject(&event->parent.parent) == RT_FALSE
mb != RT_NULL
rt_object_is_systemobject(&mb->parent.parent)
rt_object_is_systemobject(&mb->parent.parent) == RT_FALSE
rt_object_is_systemobject(&mq->parent.parent)
rt_object_is_systemobject(&mq->parent.parent) == RT_FALSE
buffer != RT_NULL
size != 0
[33m[W/kernel.device] 
(%s) assertion failed at function:%s, line number:%d 
RT_NULL
unknown
EUNKNOW
 \ | /
- RT -     Thread Operating System
15:19:29
Jan  6 2025
 / | \     %d.%d.%d build %s %s
 2006 - 2022 Copyright by RT-Thread team
end_align > begin_align
heap
heap
level == RT_EOK
(rt_uint8_t *)mem >= m->heap_ptr
(rt_uint8_t *)mem < (rt_uint8_t *)m->heap_end
small
mem init, error begin address 0x%x, and end address 0x%x
m != RT_NULL
rt_object_get_type(&m->parent) == RT_Object_Class_Memory
rt_object_is_systemobject(&m->parent)
(((rt_ubase_t)mem) & (RT_ALIGN_SIZE - 1)) == 0
(((rt_ubase_t)rmem) & (RT_ALIGN_SIZE - 1)) == 0
small_mem != RT_NULL
MEM_ISUSED(mem)
rt_object_is_systemobject(&small_mem->parent.parent)
MEM_POOL(&small_mem->heap_ptr[mem->next]) == small_mem
(rt_uint8_t *)rmem >= (rt_uint8_t *)small_mem->heap_ptr
(rt_uint8_t *)rmem < (rt_uint8_t *)small_mem->heap_end
information != RT_NULL
obj != object
object != RT_NULL
Function[%s] shall not be used in ISR
!(object->type & RT_Object_Class_Static)
thread != RT_NULL
 thread != RT_NULL
thread:%s stack overflow
warning: %s stack is close to end of stack address.
thread != RT_NULL
priority < RT_THREAD_PRIORITY_MAX
stack_start != RT_NULL
(thread->stat & RT_THREAD_STAT_MASK) == RT_THREAD_INIT
rt_object_is_systemobject((rt_object_t)thread)
rt_object_is_systemobject((rt_object_t)thread) == RT_FALSE
thread == rt_thread_self()
thread != RT_NULL
 Function[%s]: scheduler is not available
Function[%s]: interrupt is disabled
Function[%s] shall not be used before scheduler start
Function[%s] shall not be used in ISR
tick != RT_NULL
timer != RT_NULL
timeout != RT_NULL
time < RT_TICK_MAX / 2
rt_object_get_type(&timer->parent) == RT_Object_Class_Timer
rt_object_is_systemobject(&timer->parent)
rt_object_is_systemobject(&timer->parent) == RT_FALSE
 (*(rt_tick_t *)arg) < RT_TICK_MAX / 2
timer
RTTUP
RTTDOWN
 jlinkRtt
 SEGGER_RTT ADDRESS:%p 
[32m[I/feed] 
feeding 500ms timeout, odometer not change
feeding 25s timeout
stage 7: enter buffer_check
[33m[W/feed] 
feeding timeout, buffer not full
feeding stop, buffer full
Bstage8: %d.%02dmm
?feeding stop, feed extruder timeout!
 sys_uid[0] = 0x%x
sys_uid[1] = 0x%x
sys_uid[2] = 0x%x
SIGRTRED: Redirect: can't open: 
pGfeed_hub_outside
pull_back_hub
feed_top_to_hub
cmd_parse_back_stage2
filament_reset_pos
database_get_value
database_set_value
STDIN
STDOUT
STDERR
remove
_sys_open
_sys_close
_sys_read
_sys_write
_sys_ensure
_sys_seek
_sys_flen
rt_device_unregister
rt_device_destroy
rt_device_init
rt_device_open
rt_device_close
rt_device_read
rt_device_write
rt_device_control
rt_device_set_rx_indicate
rt_device_set_tx_complete
rt_device_hwtimer_isr
rt_device_hwtimer_register
rt_i2c_master_recv
i2c_bus_device_read
i2c_bus_device_write
i2c_bus_device_control
rt_i2c_bus_device_device_init
rt_completion_init
rt_completion_wait
rt_completion_done
rt_data_queue_init
rt_data_queue_push
rt_data_queue_pop
rt_data_queue_peek
rt_data_queue_reset
rt_data_queue_deinit
rt_data_queue_len
rt_ringbuffer_init
rt_ringbuffer_put
rt_ringbuffer_put_force
rt_ringbuffer_get
rt_ringbuffer_peek
rt_ringbuffer_putchar
rt_ringbuffer_putchar_force
rt_ringbuffer_getchar
rt_ringbuffer_reset
rt_ringbuffer_create
rt_ringbuffer_destroy
rt_hw_adc_register
rt_adc_read
rt_adc_enable
rt_adc_disable
rt_adc_voltage
_pin_read
_pin_write
_pin_control
rt_pin_attach_irq
rt_pin_detach_irq
rt_pin_irq_enable
rt_pin_mode
rt_pin_write
rt_pin_read
rt_pin_get
_serial_buffer_clear
_serial_poll_rx
_serial_poll_tx
_serial_int_rx
_serial_int_tx
_serial_fifo_calc_recved_len
rt_dma_recv_update_get_index
rt_dma_recv_update_put_index
_serial_dma_rx
rt_serial_init
rt_serial_open
rt_serial_close
rt_serial_read
rt_serial_write
rt_serial_control
rt_hw_serial_register
rt_hw_serial_isr
rt_hw_i2c_init
gd32_uart_configure
gd32_uart_control
gd32_uart_putc
gd32_uart_getc
GD32_UART_IRQHandler
rt_hw_usart_init
finsh_get_prompt_mode
finsh_set_prompt_mode
finsh_getchar
finsh_rx_ind
finsh_set_device
finsh_get_device
finsh_set_echo
finsh_get_echo
_msh_exec_cmd
rt_application_init
_ipc_list_suspend
rt_sem_init
rt_sem_detach
rt_sem_create
rt_sem_delete
_rt_sem_take
rt_sem_release
rt_sem_control
rt_mutex_init
rt_mutex_detach
rt_mutex_create
rt_mutex_delete
_rt_mutex_take
rt_mutex_release
rt_mutex_control
rt_event_init
rt_event_detach
rt_event_create
rt_event_delete
rt_event_send
_rt_event_recv
rt_event_control
rt_mb_init
rt_mb_detach
rt_mb_create
rt_mb_delete
_rt_mb_send_wait
rt_mb_urgent
_rt_mb_recv
rt_mb_control
rt_mq_init
rt_mq_detach
rt_mq_create
rt_mq_delete
_rt_mq_send_wait
rt_mq_urgent
_rt_mq_recv
rt_mq_control
rt_hw_cpu_shutdown
0123456789abcdef
0123456789ABCDEF
_heap_unlock
rt_system_heap_init
plug_holes
rt_smem_detach
rt_smem_alloc
rt_smem_realloc
rt_smem_free
rt_object_init
rt_object_detach
rt_object_allocate
rt_object_delete
rt_object_is_systemobject
rt_object_get_type
rt_object_find
_scheduler_stack_check
rt_schedule_insert_thread
rt_schedule_remove_thread
_thread_timeout
_thread_init
rt_thread_init
rt_thread_startup
rt_thread_detach
rt_thread_delete
rt_thread_sleep
rt_thread_delay_until
rt_thread_control
rt_thread_set_suspend_state
rt_thread_suspend_with_flag
rt_thread_resume
rt_timer_init
rt_timer_detach
rt_timer_create
rt_timer_delete
rt_timer_start
rt_timer_stop
rt_timer_control
0123456789ABCDEF
TTR REGGES
0123456789ABCDEFq3buH@CFQ!uF^t1nkRnzSSmHqfZ(@KAtB3rUpf$1BJp2eZMDc|w{
motor blocked, MS3791=%d, at8236_0=%d, at8236_1=%d, at8236_2=%d, at8236_3=%d
read_motor_info realtime                - read motor info at realtime
read_motor_info eeprom                  - read motor block info from eeprom
rfid_fil_len_per_rotation=%d, circumference_percent=%d%%, area_percent=%d%%
feed filament exceed max length, start_pos=%d, curr_pos=%d, result=%d
rfid continuous detect timeout, spool not move(move_length=%d.%02d), plese check motor
ch	count	pass	fail	
 1	%d			%d			  %d			
 2	%d			%d			  %d			
 3	%d			%d			  %d			
 4	%d			%d			  %d			
lcd temp    <temp>									-lcd set temp, such as 'lcd temp 27'
lcd SlaveNumber <SlaveNum>          -lcd set slave number, such as lcd SlaveNum 1
get_uniid
get_addr_table
online_check
set_addr
bl24cxx read <address>                  - bl24cxx read one byte
bl24cxx write <address> <write_byte>    - bl24cxx write one byte
rfid write    <card id>  <base/high>  -rfid card write init data
mat id
reserve
batch
month
year
number
supplier
color
uart1
adc1
gd32_flash
times:%d, %d error,T%d MS3791 push filament timeout or buffer timeout
     mode:     set pin mode to output/input/input_pullup/input_pulldown/output_od
     write:    write pin level(high/low or on/off) to hardware pin
pwm probe      <device name>                - probe pwm by name
pwm dead_time  <channel> <dead_time>        - set pwm dead time
pwm enable     <channel>                    - enable pwm channel
pwm enable     <channel>                   - enable pwm channel
pwm disable    <channel>                    - disable pwm channel
pwm disable    <channel>                   - disable pwm channel
pwm get        <channel>                    - get pwm channel info
pwm get        <channel>                   - get pwm channel info
pwm set        <channel> <period> <pulse>   - set pwm channel info
pwm set        <channel> <period> <pulse>  - set pwm channel info
    e.g. MSH >pwm enable -1              - PWM_CH1N complememtary
Warning: There is no enough buffer for saving data, please increase the RT_SERIAL_RB_BUFSZ option.
adc0
adc2
pwm1
pwm3
pwm4
pwm5
pwm8
i2c0
uart0
uart2
uart3
%-*.*s pri  status      sp     stack size max used left tick  error
thread
Network Interface
DAC Device
ADC Device
MTD Device
SPI Device
PWM Device
CAN Device
WLAN Device
WDT Device
Graphic Device
Sound Device
USB Slave Device
Touch Device
Block Device
Portal Device
Pin Device
PM Pseudo Device
Timer Device
Character Device
Sensor Device
Bus Device
Miscellaneous Device
Phy Device
Security Device
device
Pipe
msgqueue
timer
list threads
list devices
list semaphores
list message queues
list timers
list events
I2C Bus
USB OTG Bus
SPI Bus
SDIO Bus
USB Host Bus
list mutexs
list mailboxs
event
mutex
mailbox
rt_object_get_type(&sem->parent.parent) == RT_Object_Class_Semaphore
rt_object_get_type(&mq->parent.parent) == RT_Object_Class_MessageQueue
rt_object_get_type(&event->parent.parent) == RT_Object_Class_Event
rt_object_get_type(&mutex->parent.parent) == RT_Object_Class_Mutex
rt_object_get_type(&mb->parent.parent) == RT_Object_Class_MailBox
OK     
EIO    
EPERM  
ETRAP  
ERROR  
EBUSY  
ENOSPC 
EINVAL 
ENOMEM 
ENOSYS 
ENOENT 
Using default rt_hw_cpu_shutdown().Please consider implementing rt_hw_cpu_reset() in another file.
rt_hw_cpu_reset() doesn't support for this board.Please consider implementing rt_hw_cpu_reset() in another file.
rt_hw_us_delay() doesn't support for this board.Please consider implementing rt_hw_us_delay() in another file.
ERSFULL
EINTRPT
ETIMOUT
ERSEPTY
((small_mem->lfree == small_mem->heap_end) || (!MEM_ISUSED(small_mem->lfree)))
(rt_ubase_t)((rt_uint8_t *)mem + SIZEOF_STRUCT_MEM) % RT_ALIGN_SIZE == 0
(rt_uint8_t *)rmem >= (rt_uint8_t *)small_mem->heap_ptr && (rt_uint8_t *)rmem < (rt_uint8_t *)small_mem->heap_end
(rt_ubase_t)mem + SIZEOF_STRUCT_MEM + size <= (rt_ubase_t)small_mem->heap_end
rt_object_get_type(&small_mem->parent.parent) == RT_Object_Class_Memory
(thread->stat & RT_THREAD_SUSPEND_MASK) == RT_THREAD_SUSPEND_MASK
rt_object_get_type((rt_object_t)thread) == RT_Object_Class_Thread
reverse_detooth_set
reverse_detooth_set[en]
read_motor_info
read_motor_info
hardware_init_info
hardware_init_info
preloading
preloading
switch_mode_test
switch_mode_test[mode]
print_buffer_aging
print_buffer_aging
aging_photoelectric_CMD
aging_photoelectric_CMD[first_id][end_id]
lcd[option]
reset
reset immediate
bl24cxx
bl24cxx
odo_mag
odo_mag[option]
ahtxx_read
ahtxx_read
temp_humi
temp_humi [temp] [humi]
detooth_test
detooth_test[id][dir]
rfid
rfid[option]
mbd_test
mbd_test[motor_id]
task_test
task_test[out / back / out + back][motor_id][times]
device_uid
get device uid
check_state
check_state
at8236_test
at8236_test[id][speed][dir]
at8236_adc_test
at8236_adc_test[id]
at8236_adc_timer
at8236_adc_timer
at8236_pid_set
at8236_pid_set outkp outki outkd bkp bki bkd
led_test
led_test[white / red][id][close / open / breath / double_shan]
MS3791_test
MS3791_test[dir][speed]
MS3791_time_test
MS3791_time_test[dir][speed][time_ms]
MS3791_read_fg
MS3791_read_fg
ms3791_pid_set
ms3791_pid_set kp ki kd
buffer_test
buffer_test
box_aging_mode_test
box_aging_mode_test[first_channel][end_channel][times]
adc [option]
pin [option]
pwm [option]
help
RT-Thread shell help.
List threads in the system.
free
Show the memory usage in the system.
clear
clear the terminal screen
version
show RT-Thread version information
list
list objects
```

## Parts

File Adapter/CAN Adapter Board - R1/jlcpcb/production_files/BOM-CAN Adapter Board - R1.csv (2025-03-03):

Comment | Designator | Footprint | LCSC | Quantity
2.2u | C2 | C_0603_1608Metric | C2762602 | 1
1u | C4 | C_0402_1005Metric | C307427 | 1
Conn_01x07 | J3 | JST_GH_BM07B-GHS-TBT_1x07-1MP_P1.25mm_Vertical | C378970 | 1
Conn_01x08 | J1,J2 | JST_PH_B8B-PH-SM4-TB_1x08-1MP_P2.00mm_Vertical | C442274 | 2
TCAN332G | U2 | SOIC-8_3.9x4.9mm_P1.27mm | C73651 | 1

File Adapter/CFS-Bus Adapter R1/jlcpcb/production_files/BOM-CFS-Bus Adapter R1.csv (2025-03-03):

Comment | Designator | Footprint | LCSC | Quantity
NUP2105L | D6 | SOT-23 | C14486 | 1
100n | C3,C4,C5,C8,C9 | C_0603_1608Metric | C15849 | 5
10u_0805_X7R_10%_10V_-40C..125C_Chip-Capacitor | C10,C11,C6,C7 | C_0805_2012Metric | C15850 | 4
629722000214_pasteInHole | X1 | USB_C_Receptacle_GCT_USB4105-xx-A_16P_TopMnt_Horizontal | C165948 | 1
6p2_0603_C0G_5%_50V_-40C..125C_Chip-Capacitor | C1,C2 | C_0603_1608Metric | C1679 | 2
Conn_02x03_Top_Bottom | J1 | Molex_Micro-Fit_3.0_43045-0610_2x03-1MP_P3.00mm_Horizontal | C18202182 | 1
1k_0603_100mW_1%_E24_Chip-Resistor | R5,R8,R9 | R_0603_1608Metric | C21190 | 3
5k1 | R1,R2,R3,R4 | R_0603_1608Metric | C23186 | 4
10k_0603_100mW_1%_E24_Chip-Resistor | R6 | R_0603_1608Metric | C25804 | 1
STM32G0B1CBT | U1 | LQFP-48_7x7mm_P0.5mm | C2847904 | 1
TJA1051T3 | U3 | SOIC-8_3.9x4.9mm_P1.27mm | C38695 | 1
830108313809 | Y1 | Crystal_SMD_3225-4Pin_3.2x2.5mm | C400090 | 1
IP4234CZ6 | U4 | SC-74-6_1.55x2.9mm_P0.95mm | C455086 | 1
LED | D1,D2,D4,D5 | LED_0603_1608Metric | C5443993 | 4
KPT-1608EC | D3 | LED_0603_1608Metric | C598355 | 1
AMS1117-3.3 | U5 | SOT-223-3_TabPin2 | C6186 | 1

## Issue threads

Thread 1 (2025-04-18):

CFS Pinout

ityshchenko, 2025-04-18:
Did you have port CFS pinout? Could you add it into repo?

I'm trying to re-create *.so from k2-firmware. The modules could be loaded on Raspberry PI if you install python3.9 (same architecture). So I've pick zero w 2, connect waveshare rs485 can hat and trying to run serial_wrapper/box_wrapper there to grab some control commands.

If you want to collaborate, send me a email.

ityshchenko, 2025-04-18:
Okay. I wasn't test CANBUS but, rs485 works with 230400 baudrate.

|        | key    |        |
|--------|--------|--------|
| CAN? | CAN? | GND |
| RS485-A | RS485-B | VCC |

rubio95alex, 2025-04-19:
Hi, but the system you're proposing involves using a 485 USB port and DC power. We already have this with the upgrade kit, right? I'll probably receive it today and can test it tomorrow. Couldn't we get information by connecting the USB port to the computer and see the communication and information from the CFS?

fake-name, 2025-04-19:
Huh, I definitely reversed the connector, I didn't realize I didn't document it. It is fully specified in https://github.com/fake-name/cfs-reverse-engineering/tree/main/Adapter/CFS-Bus%20Adapter%20R1

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

The two pins you have labelled "CAN" are actually the CFS buffer status indicators - one means full, the other empty.

To get CAN, you have to use the adapter board things I designed to re-purpose the RS-485 interface as a CAN thing.

ityshchenko, 2025-04-19:
> Couldn't we get information by connecting the USB to the computer and seeing the communication and information from the CFS?

Here's lsusb output from the K1 series CFS upgrade kit.

```
Bus 001 Device 006: ID 1a86:55d3 QinHeng Electronics USB2.0 Hub
Device Descriptor:
  bLength                18
  bDescriptorType         1
  bcdUSB               1.10
  bDeviceClass            2 Communications
  bDeviceSubClass         0
  bDeviceProtocol         0
  bMaxPacketSize0         8
  idVendor           0x1a86 QinHeng Electronics
  idProduct          0x55d3
  bcdDevice            4.45
  iManufacturer           0
  iProduct                2 USB Single Serial
  iSerial                 3 589B051895
  bNumConfigurations      1
  Configuration Descriptor:
    bLength                 9
    bDescriptorType         2
    wTotalLength       0x0043
    bNumInterfaces          2
    bConfigurationValue     1
    iConfiguration          0
    bmAttributes         0x80
      (Bus Powered)
    MaxPower              138mA
    Interface Descriptor:
      bLength                 9
      bDescriptorType         4
      bInterfaceNumber        0
      bAlternateSetting       0
      bNumEndpoints           1
      bInterfaceClass         2 Communications
      bInterfaceSubClass      2 Abstract (modem)
      bInterfaceProtocol      1 AT-commands (v.25ter)
      iInterface              0
      CDC Header:
        bcdCDC               1.10
      CDC Call Management:
        bmCapabilities       0x00
        bDataInterface          1
      CDC ACM:
        bmCapabilities       0x02
          line coding and serial state
      CDC Union:
        bMasterInterface        0
        bSlaveInterface         1
      Endpoint Descriptor:
        bLength                 7
        bDescriptorType         5
        bEndpointAddress     0x83  EP 3 IN
        bmAttributes            3
          Transfer Type            Interrupt
          Synch Type               None
          Usage Type               Data
        wMaxPacketSize     0x0010  1x 16 bytes
        bInterval               1
    Interface Descriptor:
      bLength                 9
      bDescriptorType         4
      bInterfaceNumber        1
      bAlternateSetting       0
      bNumEndpoints           2
      bInterfaceClass        10 CDC Data
      bInterfaceSubClass      0
      bInterfaceProtocol      0
      iInterface              0
      Endpoint Descriptor:
        bLength                 7
        bDescriptorType         5
        bEndpointAddress     0x02  EP 2 OUT
        bmAttributes            2
          Transfer Type            Bulk
          Synch Type               None
          Usage Type               Data
        wMaxPacketSize     0x0020  1x 32 bytes
        bInterval               0
      Endpoint Descriptor:
        bLength                 7
        bDescriptorType         5
        bEndpointAddress     0x82  EP 2 IN
        bmAttributes            2
          Transfer Type            Bulk
          Synch Type               None
          Usage Type               Data
        wMaxPacketSize     0x0040  1x 64 bytes
        bInterval               0
can't get debug descriptor: Resource temporarily unavailable
Device Status:     0x0000
  (Bus Powered)
```

It has only RS485 pairs and ground. The power for CFS comes from a DC power supply. I've connected my sniffer instead of the CFS hub and made [dump](https://1drv.ms/u/c/29c9ce1e6e6c9a6e/EWKrmKH631VOsF-SLTF_KCsBIxQ5PAR7n8u3TgmhZCZW6A?e=e9wcdn). The configuration from K1 Firmware has [settings](https://github.com/ityshchenko/K1-Series-Klipper/blob/cfs_restore_missed_pyx/config/K1_MAX_CR4CU220812S12_1/box.cfg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) for `/dev/serial/by-id/usb-1a86_USB_Serial-if00-port0`.

I will try to catch some control sequences by using strace on `/dev/ttyUSB0` and it may work also on `/dev/CrealityCFS` (for Hi and K2-series).

fake-name, 2025-04-19:
It's just gonna show up as a serial device. The CFS talks (shitty, broken open-collector-ish) RS-485.

The problem is that creality has made it work by adding a bunch of compiled cython files to klipper, flagrantly violating the GPL in the process.  See `[box_wrapper.cpython-38-mipsel-linux-gnu.so](https://github.com/ityshchenko/K1-Series-Klipper/blob/cfs_restore_missed_pyx/klippy/extras/box_wrapper.cpython-38-mipsel-linux-gnu.so)` et al.

Since creality is refusing to release the source for those, and I wanted to use it with a non-compatible printer, I could either reverse engineer the protocol and figure out how to add low-speed peripherals to klipper (see https://klipper.discourse.group/t/rs485-for-low-speed-peripherals-reusing-existing-ams-feeders/22102), or find a way to make it work with mainline klipper + something like https://github.com/moggieuk/Happy-Hare or similar.

I went for the second, since it means I have to do less overall work.

ityshchenko, 2025-04-19:
> See [box_wrapper.cpython-38-mipsel-linux-gnu.so](https://github.com/ityshchenko/K1-Series-Klipper/blob/cfs_restore_missed_pyx/klippy/extras/box_wrapper.cpython-38-mipsel-linux-gnu.so) et al.

I've already inspected that [module](https://github.com/ityshchenko/K1-Series-Klipper/blob/cfs_restore_missed_pyx/klippy/extras/box_wrapper.pyx) and got all gcode commands from it.
I'd like to buy more printers like K1 SE because they’re cheap in my country, but their macros `BOX_START_PRINT` look like trying to do number two without dropping the pants. I really can't print PETG and ASA with that.

Now I'm trying to re-implement their serial_485_wrapper and box_wrapper using my ghidra finding to make my own module for Klipper.

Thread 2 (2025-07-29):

Any updates?

GONZOBOT, 2025-07-29:
I'd love to print multiple colors with my 0.2mm nozzle, but creality has ignored an issue where the CFS disregards the max volumetric flow in the slicer. So it would be awesome to k ow if this project has made progress so I and others can print with this nozzle!

fake-name, 2025-07-30:
This is entirely about using the CFS with a different printer.

Also, the CFS has no impact on anything wrt actually printing. You have a slicer issue.

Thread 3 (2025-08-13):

Current status of project

shortcord, 2025-08-13:
I saw an issue opened two weeks ago related to this but it didn't answer my question.

Since you were able to flash klipper onto the CFS and have a pretty well done pin map, is this project in a state where software configuration is the only thing left?

If not then what else is still required?

fake-name, 2025-08-15:
Yep, I have the pinouts and everything mapped and it talking to klipper. It's just software at this point.

Unfortunately, other distractions have cropped up and now I'm swamped with other stuff.

Closed 2025-08-16.

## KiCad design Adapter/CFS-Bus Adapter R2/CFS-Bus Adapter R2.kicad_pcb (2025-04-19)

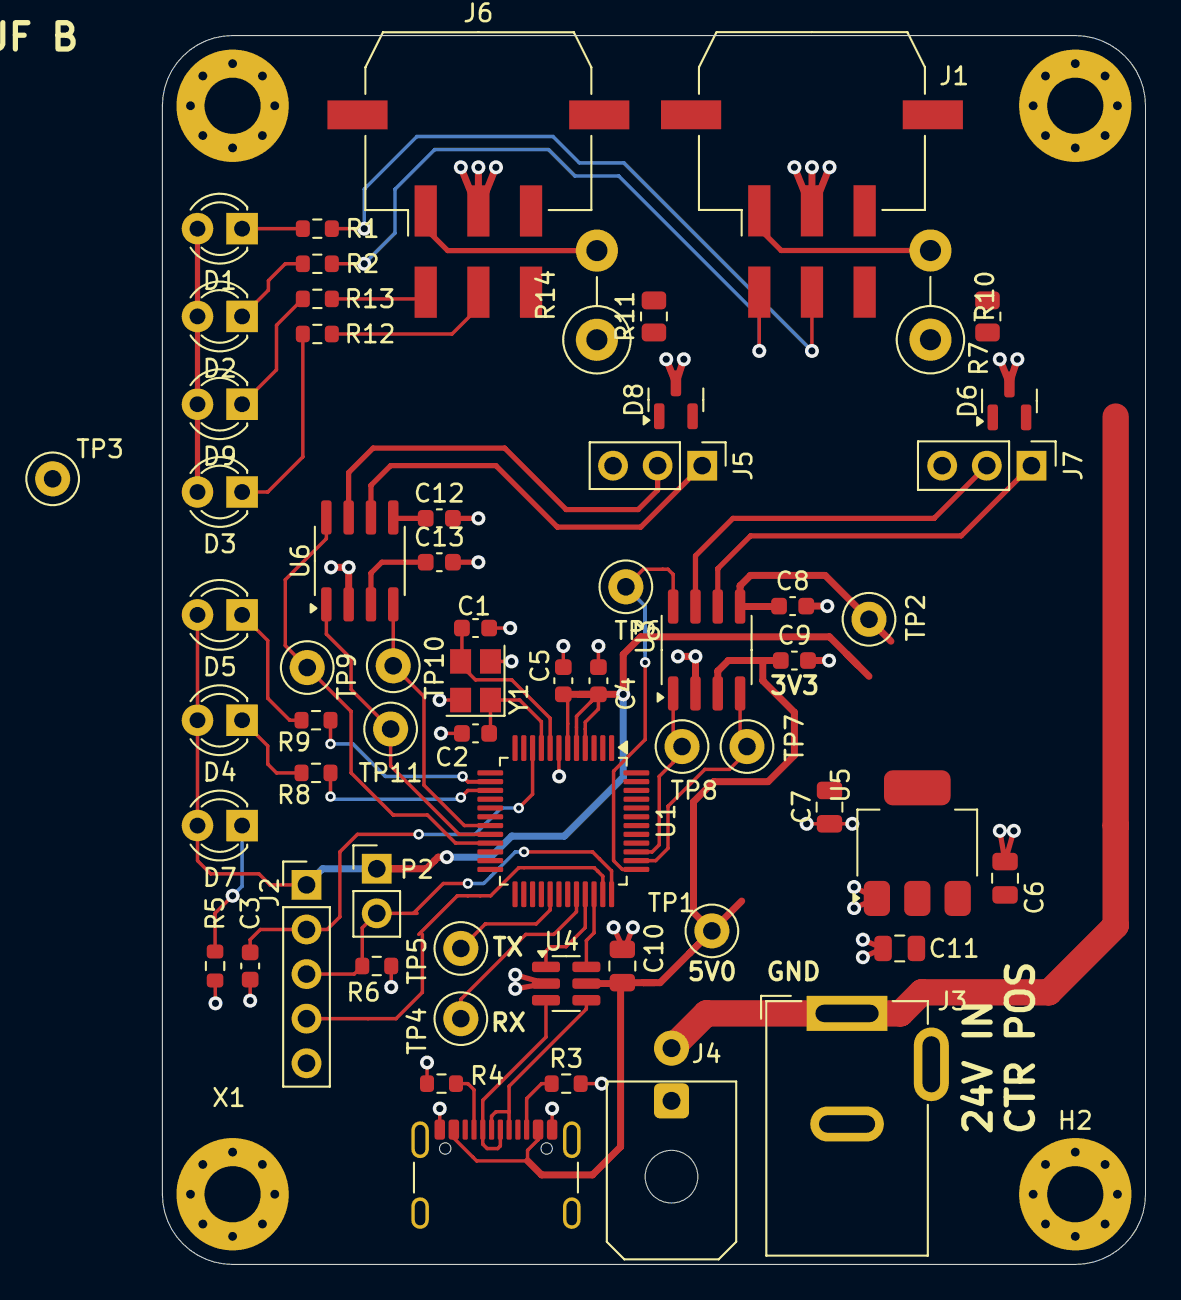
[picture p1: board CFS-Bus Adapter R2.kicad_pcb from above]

Board: 2 copper layers, 56.0 x 70.0 mm, 66 parts (0 on the bottom side), 40 nets.

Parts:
C1, C2: 6p2_0603_C0G_5%_50V_-40C..125C_Chip-Capacitor; C_0603_1608Metric
C3, C4, C5: 100n; C_0603_1608Metric
C6, C7, C10, C11: 10u_0805_X7R_10%_10V_-40C..125C_Chip-Capacitor; C_0805_2012Metric
C8, C9, C12, C13: 100n_0603_X7R_10%_50V_-40C..125C_Chip-Capacitor; C_0603_1608Metric
D1, D2, D3, D4, D5, D7, D9: LED; LED_D3.0mm
D6, D8: NUP2105L; SOT-23
H1, H2, H3, H4: MountingHole; MountingHole_3.2mm_M3_Pad_Via
J1, J6: Conn_02x03_Top_Bottom; Molex_Micro-Fit_3.0_43045-0610_2x03-1MP_P3.00mm_Horizontal
J2: Conn_01x05; PinHeader_1x05_P2.54mm_Vertical
J3: Barrel_Jack_Switch_MountingPin; BarrelJack_GCT_DCJ200-10-A_Horizontal
J4: Conn_01x02; Molex_Micro-Fit_3.0_43045-0200_2x01_P3.00mm_Horizontal
J5, J7: Conn_01x03; PinHeader_1x03_P2.54mm_Vertical
P2: CONN_01X02; PinHeader_1x02_P2.54mm_Vertical
R1, R2, R12, R13: 5k1; R_0603_1608Metric
R3, R4: 5k1_0603_100mW_1%_E24_Chip-Resistor; R_0603_1608Metric
R5, R8, R9: 1k_0603_100mW_1%_E24_Chip-Resistor; R_0603_1608Metric
R6: 10k_0603_100mW_1%_E24_Chip-Resistor; R_0603_1608Metric
R7, R11: 120R_0805_125mW_1%_E24_Chip-Resistor; R_0805_2012Metric
R10, R14: 120R_0805_125mW_1%_E24_Chip-Resistor; R_Axial_DIN0411_L9.9mm_D3.6mm_P5.08mm_Vertical
TP1, TP2, TP3: TP2.0mm; TestPoint_Loop_D1.80mm_Drill1.0mm_Beaded
TP4, TP5: TP1.0mm; TestPoint_Loop_D1.80mm_Drill1.0mm_Beaded
TP6, TP7, TP8, TP9, TP10, TP11: TestPoint; TestPoint_Loop_D1.80mm_Drill1.0mm_Beaded
U1: STM32G0B1CBT; LQFP-48_7x7mm_P0.5mm
U3, U6: TJA1051T3; SOIC-8_3.9x4.9mm_P1.27mm
U4: IP4234CZ6; SC-74-6_1.55x2.9mm_P0.95mm
U5: AMS1117-3.3; SOT-223-3_TabPin2
X1: 629722000214_pasteInHole; USB_C_Receptacle_GCT_USB4105-xx-A_16P_TopMnt_Horizontal
Y1: 830108313809; Crystal_SMD_3225-4Pin_3.2x2.5mm

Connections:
+3V3: C4.1, C5.1, C7.1, C8.1, C11.1, C12.1, D4.2 (A), D5.2 (A), D7.2 (A), J2.1, P2.1, TP2.1, U1.4 (VBAT), U1.5 (VREF+), U1.6 (VDD/VDDA), U3.5 (VIO), U5.2 (VO), U6.5 (VIO)
+5V: C6.1, C9.1, C10.1, C13.1, D1.2 (A), D2.2 (A), D3.2 (A), D9.2 (A), TP1.1, U3.3 (VCC), U4.5 (VP), U5.3 (VI), U6.3 (VCC), X1.A4 (VBUS), X1.A9 (VBUS), X1.B4 (VBUS), X1.B9 (VBUS)
+24V: J1.3, J3.1, J4.2, J6.3
/MCU/CAN1_RX: TP7.1, U1.38 (PD0), U3.4 (RXD)
/MCU/CAN1_S: TP6.1, U1.37 (PA15), U3.8 (S)
/MCU/CAN1_TX: TP8.1, U1.39 (PD1), U3.1 (TXD)
/MCU/CAN2_RX: TP10.1, U1.19 (PB0), U6.4 (RXD)
/MCU/CAN2_S: TP9.1, U1.21 (PB2), U6.8 (S)
/MCU/CAN2_TX: TP11.1, U1.20 (PB1), U6.1 (TXD)
/MCU/LED_RX: R9.2, U1.14 (PA3)
/MCU/LED_TX: R8.2, U1.15 (PA4)
/MCU/NRST: C3.1, J2.2, U1.10 (PF2/NRST)
/MCU/RX: TP4.1, U1.32 (PA10)
/MCU/SWCLK: J2.3, P2.2, R6.1, U1.36 (PA14/BOOT0)
/MCU/SWDIO: J2.4, U1.35 (PA13)
/MCU/TX: TP5.1, U1.29 (PA9)
/MCU/USB_{N}: U1.33 (PA11[PA9]), U4.1
/MCU/USB_{P}: U1.34 (PA12[PA10]), U4.6
/RS485-2-A: D8.1 (K), J5.2, J6.6, R11.1, R14.1, U6.7 (CANH)
/RS485-2-B: D8.2 (K), J5.1, J6.1, R11.2, R14.2, U6.6 (CANL)
/RS485-A: D6.1 (K), J1.6, J7.2, R7.1, R10.1, U3.7 (CANH)
/RS485-B: D6.2 (K), J1.1, J7.1, R7.2, R10.2, U3.6 (CANL)
/USB_N: U4.3, X1.A7 (DN1), X1.B7 (DN2)
/USB_P: U4.4, X1.A6 (DP1), X1.B6 (DP2)
GND: C1.1, C2.1, C3.2, C4.2, C5.2, C6.2, C7.2, C8.2, C9.2, C10.2, C11.2, C12.2, C13.2, D6.3 (A), D8.3 (A), J1.2, J2.5, J3.2, J3.3, J4.1, J5.3, J6.2, J7.3, R3.2, R4.2, R5.2, R6.2, TP3.1, U1.7 (VSS/VSSA), U3.2 (GND), U4.2 (VN), U5.1 (GND), U6.2 (GND), X1.A1 (GND), X1.B1 (GND), Y1.2 (GND), Y1.4 (GND)
unnamed: D1.1 (K), R1.1
unnamed: D2.1 (K), R2.1
unnamed: D3.1 (K), R12.1
unnamed: D4.1 (K), R8.1
unnamed: D5.1 (K), R9.1
unnamed: D7.1 (K), R5.1
unnamed: D9.1 (K), R13.1
unnamed: J1.4, R2.2
unnamed: J1.5, R1.2
unnamed: J6.4, R13.2
unnamed: J6.5, R12.2
unnamed: C1.2, U1.8 (PF0/OSC_IN), Y1.3 (C_{2})
unnamed: C2.2, U1.9 (PF1/OSC_OUT), Y1.1 (C_{1})
unnamed: R4.1, X1.A5 (CC1)
unnamed: R3.1, X1.B5 (CC2)

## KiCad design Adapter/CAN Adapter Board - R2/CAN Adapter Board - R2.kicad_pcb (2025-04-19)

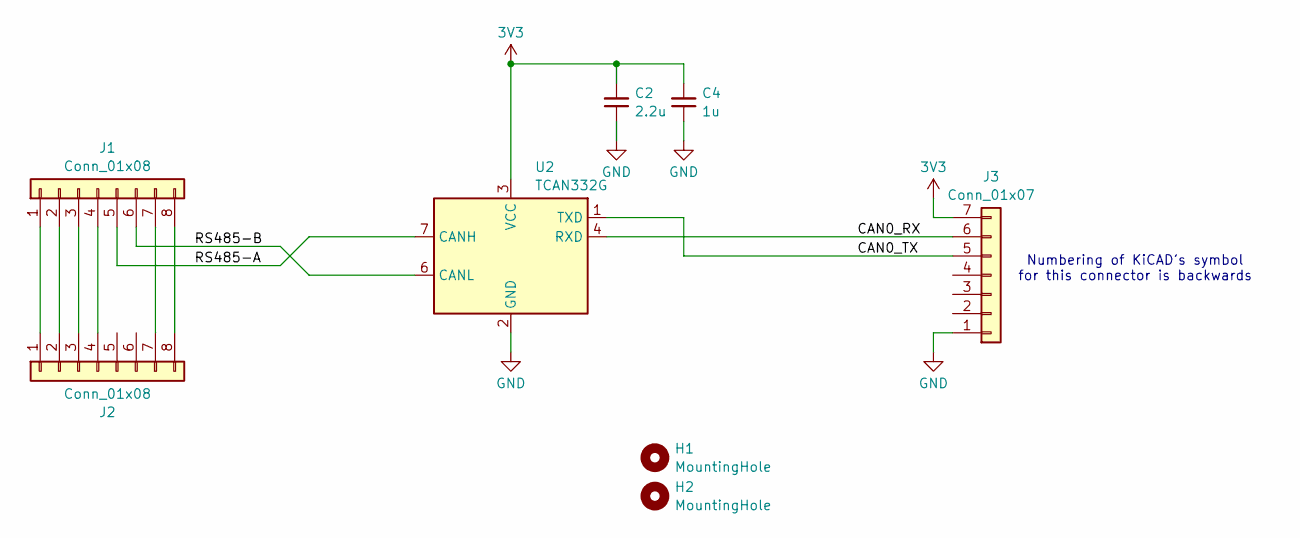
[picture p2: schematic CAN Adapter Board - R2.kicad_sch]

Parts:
C2: 2.2u; C_0603_1608Metric
C4: 1u; C_0402_1005Metric
H1, H2: MountingHole; MountingHole_3.2mm_M3_Pad_Via
J1, J2: Conn_01x08; JST_PH_B8B-PH-SM4-TB_1x08-1MP_P2.00mm_Vertical
J3: Conn_01x07; JST_GH_BM07B-GHS-TBT_1x07-1MP_P1.25mm_Vertical
U2: TCAN332G; SOIC-8_3.9x4.9mm_P1.27mm

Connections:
3V3: C2.2, C4.2, J3.7, U2.3 (VCC)
/CAN0_RX: J3.6, U2.4 (RXD)
/CAN0_TX: J3.5, U2.1 (TXD)
/RS485-A: J1.5, U2.7 (CANH)
/RS485-B: J1.6, U2.6 (CANL)
GND: C2.1, C4.1, J3.1, U2.2 (GND)
unnamed: J1.1, J2.1
unnamed: J1.2, J2.2
unnamed: J1.3, J2.3
unnamed: J1.4, J2.4
unnamed: J1.7, J2.7
unnamed: J1.8, J2.8

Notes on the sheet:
Numbering of KiCAD's symbol for this connector is backwards

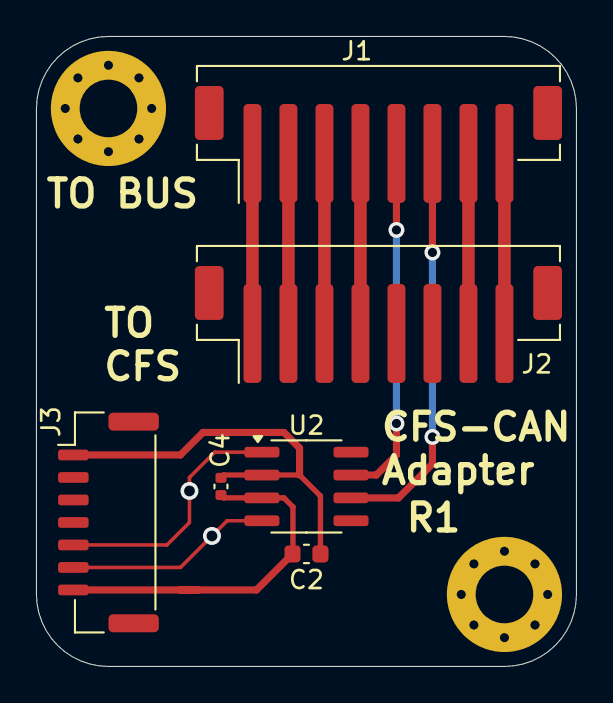
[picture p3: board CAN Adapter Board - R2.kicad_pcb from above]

Board: 2 copper layers, 30.0 x 35.0 mm, 8 parts (0 on the bottom side), 12 nets.

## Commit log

2025-02-15 Add another dump image to ghidra. This one has memory segments dumped from the real device.
2025-02-17 Add logic analyser probes of the external devices so we can do things like see how the LCD and RFID readers are configured.
2025-02-27 More connector lookups.
2025-03-03 Add various adapter boards that I just ordered
    [BOM-CAN Adapter Board - R1.csv, BOM-CFS-Bus Adapter R1.csv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]
2025-03-03 Note board files, and that creality are jerks.
2025-03-19 Add notes on the first board rev.
2025-04-19 Add second-rev of both boards with the issues fixed.
    [CAN Adapter Board - R2.kicad_pcb, CAN Adapter Board - R2.kicad_sch, CFS-Bus Adapter R1.kicad_pcb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]
